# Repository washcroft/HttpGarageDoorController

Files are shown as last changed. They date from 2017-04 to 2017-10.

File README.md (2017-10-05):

# HttpGarageDoorController (v2)
A project for an Arduino based WiFi-enabled controller, IoT/M2M enabling an ordinary garage door operator.

Demo

# About
This Arduino project allows you to directly control your garage door and/or light with HTTP requests, it exposes a very basic REST JSON API via its listening HTTP web server. Since security is important here, both API Key header and **[OAuth 1.0a](https://oauth.net/core/1.0a/) signing/authentication** is supported.

I've used a [MKR1000](https://www.arduino.cc/en/Main/ArduinoMKR1000) board which uses the [WiFi101](https://github.com/arduino-libraries/WiFi101) library, however the project also supports compilation for [ESP8266](https://en.wikipedia.org/wiki/ESP8266) boards.

The Arduino controller toggles GPIO outputs to operate the garage door (using either two separate open/close relays, or more commonly cycling the same one) and also a third output to control the garage light (another relay).

The Arduino controller also uses GPIO inputs to report the state of the garage door (two inputs from separate open/closed reed switches) and also a third input to allow the garage light to be controlled via another source (i.e. the garage door operator itself).

### HomeBridge (Apple HomeKit)
My [HomeBridge](https://github.com/nfarina/homebridge) plugin which accompanies this Arduino project can be found at [homebridge-http-garagedoorcontroller](https://github.com/washcroft/homebridge-http-garagedoorcontroller).

# Configuration

The controller is configured in the **config.h** file:

```
// Controller Config
const char MDNS_NAME[] = "garagedoorcontroller";
const char FRIENDLY_NAME[] = "Garage Door Controller";
const long DOOR_OUTPUT_PULSE_TIME = 400;
const long DOOR_OUTPUT_PULSE_DELAY_TIME = 1250;
const long DOOR_SENSOR_REACT_TIME = 3000;
const long DOOR_MAX_OPEN_CLOSE_TIME = 25000;
const long DOOR_AUTO_CLOSE_TIME = 300000;

// GPIO Pins
const int LED_OUTPUT_PIN = LED_BUILTIN;
const int DOOR_OUTPUT_OPEN_PIN = 3;
const int DOOR_OUTPUT_CLOSE_PIN = 3;
const int LIGHT_OUTPUT_PIN = 2;
const int LIGHT_INPUT_PIN = 1;
const int SENSOR_OPEN_INPUT_PIN = 5;
const int SENSOR_CLOSED_INPUT_PIN = 4;

// ADVANCED - DEFAULTS ARE NORMALLY OK
// Network Config
const long HTTP_SERVER_PORT = 80;
const long HTTP_REQUEST_TIMEOUT = 4000;
const long HTTP_REQUEST_BUFFER_SIZE = 512;
const long WIFI_CONNECTION_TIMEOUT = 10000;

// OAuth Config
const uint16_t OAUTH_NONCE_SIZE = 24;
const uint16_t OAUTH_NONCE_HISTORY = 255;
const uint16_t OAUTH_TIMESTAMP_VALIDITY_WINDOW = 300000;
```

### Variables:

* MDNS_NAME

  The mDNS hostname the controller should publish (exclude .local)

* FRIENDLY_NAME

  The friendly name for the controller

* DOOR_OUTPUT_PULSE_TIME

  The amount of time in milliseconds the GPIO output is kept HIGH when operated (simulated button press)

* DOOR_OUTPUT_PULSE_DELAY_TIME

  The amount of time in milliseconds to wait before the garage door operator will respond to a second triggering of the GPIO output

* DOOR_SENSOR_REACT_TIME

  The amount of time in milliseconds the open/closed sensors take to react to the garage door opening/closing

* DOOR_MAX_OPEN_CLOSE_TIME

  The maximum amount of time in milliseconds the garage door should take to open or close (used to detect a fault status, add a few seconds of margin)

* DOOR_AUTO_CLOSE_TIME

  The maximum amount of time in milliseconds the garage door should be left open before automatically closing, or zero to disable automatic closing (default 300000 = 5 minutes)

* LED_OUTPUT_PIN

  The GPIO output pin connected to the 'network connected' status LED (optional, default LED_BUILTIN)

* DOOR_OUTPUT_OPEN_PIN

  The GPIO output pin connected to the garage door open relay trigger

* DOOR_OUTPUT_CLOSE_PIN

  The GPIO output pin connected to the garage door close relay trigger (set the same as DOOR_OUTPUT_OPEN_PIN if the operator doesn't use separate open/close triggers)

* LIGHT_OUTPUT_PIN

  The GPIO output pin connected to the garage light relay trigger

* LIGHT_INPUT_PIN

  The GPIO input pin connected to the external garage light trigger (optional)

* SENSOR_OPEN_INPUT_PIN

  The GPIO input pin connected to the reed switch at the garage door open position

* SENSOR_CLOSED_INPUT_PIN

  The GPIO input pin connected to the reed switch at the garage door closed position

* HTTP_SERVER_PORT

  The TCP port the HTTP web server should listen on (default 80)

* HTTP_REQUEST_TIMEOUT

  The amount of time in milliseconds a request is allowed to take before closing it (default 4000)

* HTTP_REQUEST_BUFFER_SIZE

  The buffer size to allocate for each incoming HTTP request (default 512)

* WIFI_CONNECTION_TIMEOUT

  The amount of time in milliseconds a WiFi connection can wait to setup before retrying (default 10000)

* OAUTH_NONCE_SIZE

  The size of nonces to retain in memory to prevent replay attacks (default 24)

* OAUTH_NONCE_HISTORY

  The number of nonces to retain in memory to prevent replay attacks (default 255)

* OAUTH_TIMESTAMP_VALIDITY_WINDOW

  The amount of time drift allowed when validating timestamps, since the controller and requester's clocks won't be in exact sync (default 300000 = 5 minutes)

You will also need to add a **secret.h** file to your project containing your sensitive configuration:

```
const char WIFI_SSID[] = "WiFi";
const char WIFI_PASSWORD[] = "MyPassword";
const char OTA_UPDATER_PASSWORD[] = "MyPassword";

const char HTTP_SERVER_APIKEY_HEADER[] = "MyPassword";

const char HTTP_SERVER_OAUTH_CONSUMER_KEY[] = "MyOAuthConsumerKey";
const char HTTP_SERVER_OAUTH_CONSUMER_SECRET[] = "MyOAuthConsumerSecret";
```

### Variables:

* WIFI_SSID

  The WiFi network SSID to connect to

* WIFI_PASSWORD

  The WiFi network password to authenticate the connection

* OTA_UPDATER_PASSWORD

  The password which unlocks over-the-air (OTA) firmware updating in the Arduino IDE

* HTTP_SERVER_APIKEY_HEADER

  The API key which must exist in the X-API-Key HTTP header to authenticate the request (optional, 32 alphanumeric characters recommended or empty string to disable)

* HTTP_SERVER_OAUTH_CONSUMER_KEY

  The OAuth consumer key to be used for OAuth authentication and signing, similar to a username (optional, 32 alphanumeric characters recommended or empty string to disable)

* HTTP_SERVER_OAUTH_CONSUMER_SECRET

  The OAuth consumer secret to be used for OAuth authentication and signing, similar to a password (optional, 64 alphanumeric characters recommended or empty string to disable)

# Debugging

Debug logging can be enabled in the **compile.h** file:

```
#define LOG_LEVEL 0 // ERROR = 1, INFO = 2, DEBUG = 3, VERBOSE = 4, TRACE = 5
```

Increasing the LOG_LEVEL will increase the amount of Serial output to assist with debugging. Ensure this is set back to 0 for production deployment to conserve resources.

# Example Circuit Diagram

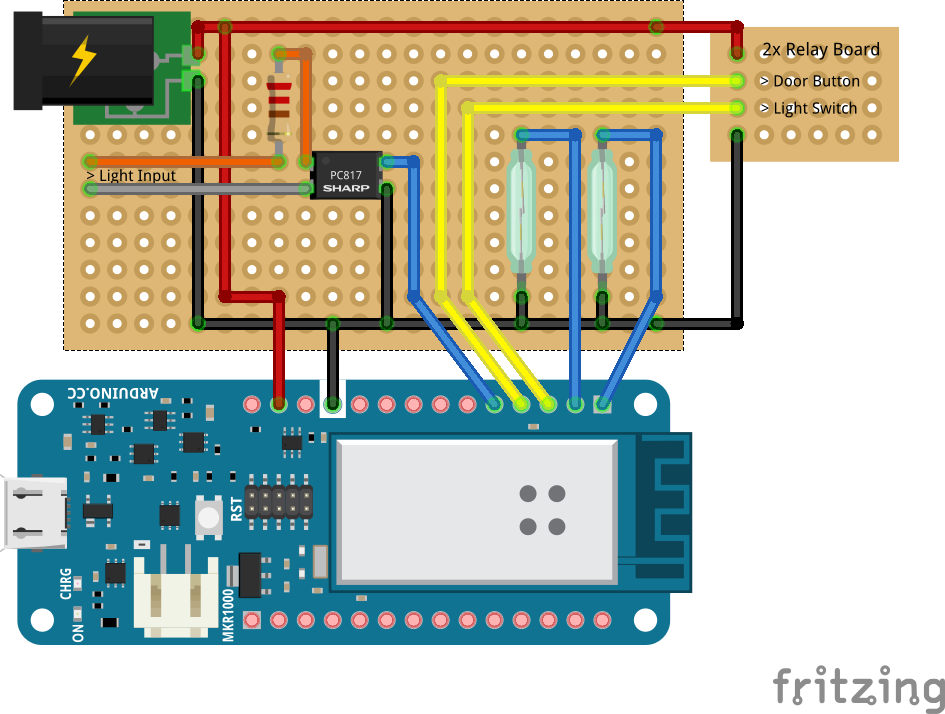
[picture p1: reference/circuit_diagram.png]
Example Circuit Diagram


# REST API Documentation

If the *HTTP_SERVER_APIKEY_HEADER* variable defined in your *secret.h* file is set, all API requests must include the HTTP header **X-API-Key** with that value.

If the *HTTP_SERVER_OAUTH_CONSUMER_KEY* and *HTTP_SERVER_OAUTH_CONSUMER_SECRET* variables defined in your *secret.h* file are set, all API requests must include the OAuth signing parameters in the querystring.

The returned content type will always be **application/json**.

**Note:** It is always recommended to use OAuth to maintain high security, otherwise intercepted HTTP requests on the network would reveal security keys and passwords that could be reused at a later date. Intercepted HTTP requests authorised with OAuth don't reveal any secrets and the same request (i.e. open door) cannot be "replayed" at a later date.

There are plenty of OAuth clients and libraries available, particularly for communicating with the Twitter API as it uses the same scheme. See Twitter developer documentation "[Creating a signature](https://developer.twitter.com/en/docs/basics/authentication/guides/creating-a-signature)".

**Device Info**
----
Returns a JSON payload reporting various running parameters.

* **URL**

  /device

* **Method:**

  `GET`
  
* **URL Params**

  None

* **Success Response:**

  * **Code:** 200 OK <br />
    **Content:**
    
    ```json
    {
      "mdns": "garagedoorcontroller",
      "name": "Garage Door Controller",
      "model": "GARAGEDOOR",
      "firmware": "2.0.0",
      "ip": "10.0.1.152",
      "mac": "ab:3d:f5:aa:a0:22"
    }
    ```
	
**Controller Status**
----
Returns a JSON payload reporting various input/output states.

* **URL**

  /controller

* **Method:**

  `GET`
  
* **URL Params**

  None

* **Success Response:**

  * **Code:** 200 OK <br />
    **Content:**
    
    ```json
    {
      "result": 200,
      "success": true,
      "message": "OK",
      "light-input": false,
      "light-requested": false,
      "light-state": false,
      "sensor-open": false,
      "sensor-closed": false,
      "door-state": "closing"
    }
    ```
 
* **Error Response:**

  * **Code:** 401 Unauthorized <br />
    **Content:**
    
    ```json
    {
      "result": 401,
      "success": false,
      "message": "The requested resource was unauthorized."
    }
    ```

**Control Door**
----
Controls the configured door GPIO output pin with a brief pulse (pulse time configured with *DOOR_OUTPUT_PULSE_TIME*).

* **URL**

  /controller/door/:action

* **Method:**

  `PUT`
  
* **URL Params**

   **Required:**

   `action=[open|close]`

* **Success Response:**

  * **Code:** 202 Accepted <br />
    **Content:**
    
    ```json
    {
      "result": 202,
      "success": true,
      "message": "Accepted"
    }
    ```
 
* **Error Response:**

  * **Code:** 401 Unauthorized <br />
    **Content:**
    
    ```json
    {
      "result": 401,
      "success": false,
      "message": "The requested resource was unauthorized."
    }
    ```

**Control Light**
----
Controls the configured light GPIO output pin and latches.

*Note: If the configured light GPIO input pin is HIGH, it will always override this.*

* **URL**

  /controller/light/:action

* **Method:**

  `PUT`
  
* **URL Params**

   **Required:**

   `action=[on|off]`

* **Success Response:**

  * **Code:** 202 Accepted <br />
    **Content:**
    
    ```json
    {
      "result": 202,
      "success": true,
      "message": "Accepted"
    }
    ```
 
* **Error Response:**

  * **Code:** 401 Unauthorized <br />
    **Content:**
    
    ```json
    {
      "result": 401,
      "success": false,
      "message": "The requested resource was unauthorized."
    }
    ```

# Dependencies, Credits and Licensing
### MKR1000:
- [WiFi101](https://github.com/arduino-libraries/WiFi101) (Copyright (c) Arduino LLC. All right reserved. - GNU LGPL v2.1)
- [WiFi101OTA](https://github.com/arduino-libraries/WiFi101OTA) (Copyright (c) Arduino LLC. All right reserved. - GNU LGPL v2.1)

**Note:** WiFi101OTA does not currently support mDNS hostname resolution, so you will only be able to access the controller via its IP address. I have submitted [Pull Request #3](https://github.com/arduino-libraries/WiFi101OTA/pull/3) for this feature to be included, until then you may choose to [use my version](https://github.com/washcroft/WiFi101OTA/tree/mDNSResponder).

### ESP8266:
- [Arduino for ESP8266](https://github.com/esp8266/Arduino) (Copyright (c) Various. All right reserved. - GNU LGPL v2.1)
- [ArduinoOTA](https://github.com/esp8266/Arduino/tree/master/libraries/ArduinoOTA) (Copyright (c) Various. All right reserved. - GNU LGPL v2.1)

### Libraries:
- [ArduinoJson](https://github.com/bblanchon/ArduinoJson) (Copyright (c) 2014-2017 Benoit BLANCHON - MIT)
- [Bounce2](https://github.com/thomasfredericks/Bounce2) (Copyright (c) 2013 thomasfredericks - MIT)

### Bundled:
- [Sha](https://github.com/Cathedrow/Cryptosuite) (Peter Knight - Public Domain)
- [Base64](https://github.com/adamvr/arduino-base64) (Copyright (c) 2013 Adam Rudd - MIT)
- [HashMap](https://github.com/WiringProject/Wiring/tree/master/framework/libraries/HashMap) (Copyright (c) 2011 Alexander Brevig - GNU LGPL v3.0)
- Clock (Copyright (c) 2017 Warren Ashcroft - MIT)
- HttpWebServer (Copyright (c) 2017 Warren Ashcroft - MIT)
- Utilities (Copyright (c) 2017 Warren Ashcroft - MIT)
- WiFiHelper (Copyright (c) 2017 Warren Ashcroft - MIT)

# License
```
MIT License

Copyright (c) 2017 Warren Ashcroft

Permission is hereby granted, free of charge, to any person obtaining a copy
of this software and associated documentation files (the "Software"), to deal
in the Software without restriction, including without limitation the rights
to use, copy, modify, merge, publish, distribute, sublicense, and/or sell
copies of the Software, and to permit persons to whom the Software is
furnished to do so, subject to the following conditions:

The above copyright notice and this permission notice shall be included in all
copies or substantial portions of the Software.

THE SOFTWARE IS PROVIDED "AS IS", WITHOUT WARRANTY OF ANY KIND, EXPRESS OR
IMPLIED, INCLUDING BUT NOT LIMITED TO THE WARRANTIES OF MERCHANTABILITY,
FITNESS FOR A PARTICULAR PURPOSE AND NONINFRINGEMENT. IN NO EVENT SHALL THE
AUTHORS OR COPYRIGHT HOLDERS BE LIABLE FOR ANY CLAIM, DAMAGES OR OTHER
LIABILITY, WHETHER IN AN ACTION OF CONTRACT, TORT OR OTHERWISE, ARISING FROM,
OUT OF OR IN CONNECTION WITH THE SOFTWARE OR THE USE OR OTHER DEALINGS IN THE
SOFTWARE.
```

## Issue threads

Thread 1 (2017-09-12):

Software for ESP8266 NodeMCU

Diederik98, 2017-09-12:
Hi,

Thanks for your great plugin and arduino code! I copied your version and adjusted it to use it with an ESP8266. I also added OTA support.

I'll post it as attachment.

Kind regards!

[OTA ESP8266 http garagedoor.zip](https://github.com/washcroft/HttpGarageDoorController/files/1297360/OTA.ESP8266.http.garagedoor.zip)

jeylites, 2017-09-22:
@Diederik98

Thanks for the ESP8266 support. I tried to compile today but was stoped with an error. I seem to be missing a Tasker.h file.

Build options changed, rebuilding all
/Users/Documents/Arduino/ESP8266_HTTP_OTA_GARAGEDOOR/ESP8266_HTTP_OTA_GARAGEDOOR.ino:8:20: fatal error: Tasker.h: No such file or directory
 #include <Tasker.h>
                    ^
compilation terminated.
exit status 1
Error compiling for board Generic ESP8266 Module.

Diederik98, 2017-09-22:
Glad you liked it!

You have to add the library first.
You can find it on the main page under Dependencies.

Tasker, Bounce have to be installed. I'm not sure ArduinoJson is one of the standard libraries. Otherwise you also need to install that library.

jeylites, 2017-09-22:
I included the library through Arduino Manage library. It complies but I don't see any MQTT traffic on serial monitor.

I see it has created a device in my router. The web page shows the following.

{ "result": 401, "success": false, "message": "The requested resource was unauthorised." }

Diederik98, 2017-09-22:
I always tested it with the homebridge accessory, because I don't know that much about http headers. Use same api key and check the homebridge log. Have you uncommented '#define DEBUG 1' in your code? Try to use a print statement when the garage is opened and toggle it with your accessory on your iOS device.

jeylites, 2017-09-22:
I uncommented #define DEBUG 1 and I was able to see the MQTT messages. It's working now.

I just want to confirm the pins connection below. I connect a relay to light & door, the light works however not the door.

What are the #define numbers corresponding to e.g.: #define D1 5 ?

DOOR RELAY OPEN/CLOSE = D2
SENSOR REED SWITCH OPEN = D8
SENSOR REED SWITCH CLOSE = D0
LIGHT = D4

Sketch "
#define D0 16
#define D1 5
#define D2 4
#define D3 0
#define D4 2
#define D5 14
#define D6 12
#define D7 13
#define D8 15
#define D9 3
#define D10 1
// LED ON ESP8266 on D4 or GPIO 2
const int LED_OUTPUT_PIN = D4;
const int DOOR_OUTPUT_OPEN_PIN = D2;
const int DOOR_OUTPUT_CLOSE_PIN = D2;
const int LIGHT_OUTPUT_PIN = D4;
const int LIGHT_INPUT_PIN = D1;
// not used, but I gave it a random pin, I did not want to change the code that much.
const int SENSOR_OPEN_INPUT_PIN = D8;
const int SENSOR_CLOSED_INPUT_PIN = D0;
"

Diederik98, 2017-09-26:
I'm sorry for my late answer. I hope it's working now! I used a NodeMCU ESP8266 and each pin had a label. I did that to make the wiring for my device easier.
I think the sensor is HIGH when opened, just print the value to be sure.

washcroft, 2017-10-04:
Thank you Diederik98. I have just released v2.0.0 of this project which includes support for ESP8266 boards (and more).

Closed 2017-10-04.

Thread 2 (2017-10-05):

Error compiling - Secret.h

jeylites, 2017-10-05:
Is my secret.h file correct?

**Secret.h**

const char WIFI_SSID[] = "HELLO";
const char WIFI_PASSWORD[] = "12345678";
const char OTA_UPDATER_PASSWORD[] = "12345678";

const char HTTP_SERVER_APIKEY_HEADER[] = "12345678";

const char HTTP_SERVER_OAUTH_CONSUMER_KEY[] = "HELLO";
const char HTTP_SERVER_OAUTH_CONSUMER_SECRET[] = "ROUTER";

**ERROR MESSAGE**
`Arduino: 1.8.3 (Mac OS X), Board: "Generic ESP8266 Module, Serial, 80 MHz, 40MHz, DOUT, 115200, 1M (no SPIFFS), ck, Disabled, None"

In file included from sketch/GarageDoorController.h:14:0,
                 from /Users/J/Documents/Arduino/Portable/HttpGarageDoorController/HttpGarageDoorController.ino:46:
secret.h:1: error: redefinition of 'const char WIFI_SSID []'
 const char WIFI_SSID[] = "HELLO";
                      ^
In file included from /Users/J/Documents/Arduino/Portable/HttpGarageDoorController/HttpGarageDoorController.ino:44:0:
secret.h:1: error: 'const char WIFI_SSID [6]' previously defined here
 const char WIFI_SSID[] = "HELLO";
            ^
In file included from sketch/GarageDoorController.h:14:0,
                 from /Users/J/Documents/Arduino/Portable/HttpGarageDoorController/HttpGarageDoorController.ino:46:
secret.h:2: error: redefinition of 'const char WIFI_PASSWORD []'
 const char WIFI_PASSWORD[] = "12345678";
                          ^
In file included from /Users/J/Documents/Arduino/Portable/HttpGarageDoorController/HttpGarageDoorController.ino:44:0:
secret.h:2: error: 'const char WIFI_PASSWORD [9]' previously defined here
 const char WIFI_PASSWORD[] = "12345678";
            ^
In file included from sketch/GarageDoorController.h:14:0,
                 from /Users/J/Documents/Arduino/Portable/HttpGarageDoorController/HttpGarageDoorController.ino:46:
secret.h:3: error: redefinition of 'const char OTA_UPDATER_PASSWORD []'
 const char OTA_UPDATER_PASSWORD[] = "12345678";
                                 ^
In file included from /Users/J/Documents/Arduino/Portable/HttpGarageDoorController/HttpGarageDoorController.ino:44:0:
secret.h:3: error: 'const char OTA_UPDATER_PASSWORD [9]' previously defined here
 const char OTA_UPDATER_PASSWORD[] = "12345678";
            ^
In file included from sketch/GarageDoorController.h:14:0,
                 from /Users/J/Documents/Arduino/Portable/HttpGarageDoorController/HttpGarageDoorController.ino:46:
secret.h:5: error: redefinition of 'const char HTTP_SERVER_APIKEY_HEADER []'
 const char HTTP_SERVER_APIKEY_HEADER[] = "12345678";
                                      ^
In file included from /Users/J/Documents/Arduino/Portable/HttpGarageDoorController/HttpGarageDoorController.ino:44:0:
secret.h:5: error: 'const char HTTP_SERVER_APIKEY_HEADER [9]' previously defined here
 const char HTTP_SERVER_APIKEY_HEADER[] = "12345678";
            ^
In file included from sketch/GarageDoorController.h:14:0,
                 from /Users/J/Documents/Arduino/Portable/HttpGarageDoorController/HttpGarageDoorController.ino:46:
secret.h:7: error: redefinition of 'const char HTTP_SERVER_OAUTH_CONSUMER_KEY []'
 const char HTTP_SERVER_OAUTH_CONSUMER_KEY[] = "HELLO";
                                           ^
In file included from /Users/J/Documents/Arduino/Portable/HttpGarageDoorController/HttpGarageDoorController.ino:44:0:
secret.h:7: error: 'const char HTTP_SERVER_OAUTH_CONSUMER_KEY [6]' previously defined here
 const char HTTP_SERVER_OAUTH_CONSUMER_KEY[] = "HELLO";
            ^
In file included from sketch/GarageDoorController.h:14:0,
                 from /Users/J/Documents/Arduino/Portable/HttpGarageDoorController/HttpGarageDoorController.ino:46:
secret.h:8: error: redefinition of 'const char HTTP_SERVER_OAUTH_CONSUMER_SECRET []'
 const char HTTP_SERVER_OAUTH_CONSUMER_SECRET[] = "ROUTER";
                                              ^
In file included from /Users/J/Documents/Arduino/Portable/HttpGarageDoorController/HttpGarageDoorController.ino:44:0:
secret.h:8: error: 'const char HTTP_SERVER_OAUTH_CONSUMER_SECRET [7]' previously defined here
 const char HTTP_SERVER_OAUTH_CONSUMER_SECRET[] = "ROUTER";
            ^
exit status 1
redefinition of 'const char WIFI_SSID []'

This report would have more information with
"Show verbose output during compilation"
option enabled in File -> Preferences.
`

washcroft, 2017-10-05:
This was caused by the **secret.h** file being included twice within the project, this is now fixed.

jeylites, 2017-10-05:
Will test it again :)

Closed 2017-10-05.

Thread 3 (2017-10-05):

Unable to debug & D1 Mini GPIO

jeylites, 2017-10-05:
Unable to see if device connected to the router or not, previously, I was able to see the messages after  uncommented '#define DEBUG

Here is the changes I made...
#define LOG_LEVEL 3 // ERROR = 1, INFO = 2, DEBUG = 3, VERBOSE = 4, TRACE = 5

**Baud: 115200**
ets Jan  8 2013,rst cause:4, boot mode:(3,6)

wdt reset
load 0x4010f000, len 1384, room 16
tail 8
chksum 0x2d
csum 0x2d
v3de0c112
~ld

I'm currently using a Wemos D1 mini for this project,
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

Are the GPIO pin the same as the sketch

// GPIO Pins
const uint8_t LED_OUTPUT_PIN = LED_BUILTIN;
const uint8_t DOOR_OUTPUT_OPEN_PIN = 3;
const uint8_t DOOR_OUTPUT_CLOSE_PIN = 3;
const uint8_t LIGHT_OUTPUT_PIN = 2;
const uint8_t LIGHT_INPUT_PIN = 1;
const uint8_t SENSOR_OPEN_INPUT_PIN = 5;
const uint8_t SENSOR_CLOSED_INPUT_PIN = 4;

washcroft, 2017-10-05:
Hello,
The pins in the example config won't work on the ESP8266, as they're what I used on a MKR1000. That's why it's currently crashing, before it's even started during pin setup.

I have just tested this with Wemos D1 mini, and here are some example pins that work for that board:

```
// GPIO Pins
const uint8_t LED_OUTPUT_PIN = LED_BUILTIN;
const uint8_t DOOR_OUTPUT_OPEN_PIN = D1;     // D1 = pin 16
const uint8_t DOOR_OUTPUT_CLOSE_PIN = D1;    // D1 = pin 16
const uint8_t LIGHT_OUTPUT_PIN = D2;         // D2 = pin 4
const uint8_t LIGHT_INPUT_PIN = D5;          // D5 = pin 14
const uint8_t SENSOR_OPEN_INPUT_PIN = D6;    // D6 = pin 12
const uint8_t SENSOR_CLOSED_INPUT_PIN = D7;  // D7 = pin 13
```

Best Regards,
Warren

Closed 2017-10-06.

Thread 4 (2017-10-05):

API Key header authorization FAILURE - header mismatch & Trigger Hi/Lo

jeylites, 2017-10-05:
I'm making progress washcroft... I'm currently stuck on the API key header authentication

What is the relation for the following

```
HTTP_SERVER_APIKEY_HEADER[] = "MyOAuthConsumerKey";
HTTP_SERVER_OAUTH_CONSUMER_KEY[] = "MyOAuthConsumerKey";
HTTP_SERVER_OAUTH_CONSUMER_SECRET[] = "MyOAuthConsumerSecret";
```

AND

```
"httpHeaderName": "MyPassword",
"httpHeaderValue": "MyPassword",

```

WiFi Connection Lost - Connecting
Finding WiFi hardware......found!
Connecting to WiFi network...{"result":200,"success":true,"message":"OK","light-input":false,"light-requested":false,"light-state":false,"sensor-open":true,"sensor-closed":false,"door-state":"open"}
{"result":200,"success":true,"message":"OK","light-input":false,"light-requested":false,"light-state":false,"sensor-open":true,"sensor-closed":false,"door-state":"open"}
connected to HELLO
Obtaining IP address...obtained 192.xxx.xxx.xxx
WiFi Connection Complete

SSID: HELLO
Signal Strength (RSSI): -63 dBm
Client MAC: xc:cf:xf:fx:bx:ex
Station MAC: ax:bx:ex:ec:5x:ce
Client IP Address: 192.xxx.xxx.xxx
Gateway IP Address: 192.xxx.xxx.xxx
mDNS Hostname: garagedoorcontroller.local

Starting OTA updater / mDNS responderStarting HTTP web server...started!
Initalising clock...initalised at 2017-10-05 17:16:28 UTC
{"result":200,"success":true,"message":"OK","light-input":false,"light-requested":false,"light-state":false,"sensor-open":true,"sensor-closed":false,"door-state":"open"}
{"result":200,"success":true,"message":"OK","light-input":false,"light-requested":false,"light-state":false,"sensor-open":true,"sensor-closed":false,"door-state":"open"}

Accepted new client connection from 192.xxx.xxx.xxx:49178
GET /controller HTTP/1.1
MyOAuthConsumerKey: MyOAuthConsumerKey
host: garagedoorcontroller.local
Connection: close

**API Key header authorisation FAILURE - header mismatch**
HTTP/1.1 401 Unauthorized
Content-Type: application/json
Connection: close

**Secret.h**
```
const char WIFI_SSID[] = "HELLO";
const char WIFI_PASSWORD[] = "12345678";
const char OTA_UPDATER_PASSWORD[] = "MyPassword";

const char HTTP_SERVER_APIKEY_HEADER[] = "MyOAuthConsumerKey";

const char HTTP_SERVER_OAUTH_CONSUMER_KEY[] = "MyOAuthConsumerKey";
const char HTTP_SERVER_OAUTH_CONSUMER_SECRET[] = "MyOAuthConsumerSecret";

```

**Homebridge Config.**

```
{
	"accessories": [{
		"accessory": "HttpGarageDoorController",
		"name": "Garage Door",
		"lightName": "Garage Light",

		"doorOperationSeconds": 0,

		"httpHost": "garagedoorcontroller.local",
		"httpPort": 80,
		"httpSsl": false,
		"httpStatusPollMilliseconds": 4000,
		"httpRequestTimeoutMilliseconds": 10000,

		"httpHeaderName": "MyPassword",
		"httpHeaderValue": "MyPassword",

		"oauthAuthentication": true,
		"oauthSignatureMethod": "HMAC-SHA256",
		"oauthConsumerKey": "MyOAuthConsumerKey",
		"oauthConsumerSecret": "MyOAuthConsumerSecret",
		"oauthToken": "MyOAuthToken",
		"oauthTokenSecret": "MyOAuthTokenSecret",

		"apiConfig": {
			"apiType": "HttpGarageDoorController"
		}
	}]
}

```

washcroft, 2017-10-05:
When using the HomeBridge module with this Arduino project, ```httpHeaderName``` should be "X-API-Key" - this isn't clear so I'll add that to the docs.

```oauthConsumerKey``` and ```oauthConsumerSecret``` should match in both HomeBridge module and Arduino project.

```oauthToken``` and ```oauthTokenSecret``` should be empty "" because they're not using in the Arduino project.

jeylites, 2017-10-06:
@washcroft

After some tinkering, I manage to get it working. The APIKEY HEADER threw me off. I was thinking "MyPassword" was supposed to be the same password as OTA in the Arduino secret.h sketch but what it really meant was "MyAPIKey".

```
**Secret.h**
const char HTTP_SERVER_APIKEY_HEADER[] = "MyPassword";
**Config.json**
"httpHeaderValue": "MyAPIKey"

```
**RELAY hi/lo trigger**
Is there a way to set the relay outputs to LOW-level trigger. The reason I'm asking is that the relays go from HI to LO after the Wemmos D1 mini comes out from a power cycle or reset which in turn opens the garage door.

**API**
What are the Json API and Generic / Plain API usage and difference?

**Timings**
`DOOR_SENSOR_REACT_TIME` & `DOOR_MAX_OPEN_CLOSE_TIME `

Should REACT time be the same or as MAX time or by half?
React time do you mean as how fast the state changes from one or the other?

Thank you.

washcroft, 2017-10-08:
> Is there a way to set the relay outputs to LOW-level trigger. The reason I'm asking is that the relays go from HI - LO - HI after the Wemmos D1 mini comes out from a power cycle or reset which in turn opens the garage door.

The controller brings the relay pin ```HIGH``` for the ```DOOR_OUTPUT_PULSE_DELAY_TIME``` time and then puts it back ```LOW``` (to simulate a button press). How are you connecting it to your motor controller if LOW triggers it?

> What are the Json API and Generic / Plain API usage and difference?

The homebridge-http-garagedoorcontroller is designed to support other integrations, but if you're using this HttpGarageDoorController project, you don't need to use those since setting ```apiType``` to HttpGarageDoorController configures the API correctly.

> Should REACT time be the same or as MAX time or by half?

Some door open/closed sensors "bounce" or "flicker" when changing state (i.e. magnetic reed switches), the ```DOOR_SENSOR_REACT_TIME``` setting sets how long the sensors have to settle in their current state before using their values.

```DOOR_MAX_OPEN_CLOSE_TIME``` sets how long the motor usually takes to open or close the door. If the door hasn't completely opened or closed during this time (as indicated by the sensors), then the controller can report the door the "stopped" moving and is therefore left partially open.

> Lastly, On Homebridge to change the Icon from a garage to a switch, do I change the MDNS NAME & FRIENDLY to = lock or switch?

No, these fields just identify the devices on the network. Currently, the module will always report the unit to HomeKit as a "Garage Door service". This may change with a feature update soon.

jeylites, 2017-10-08:
Is there a way to set the relay outputs to LOW-level trigger. The reason I'm asking is that the relays go from HI - LO - HI after the Wemmos D1 mini comes out from a power cycle or reset which in turn opens the garage door.

> The controller brings the relay pin HIGH for the DOOR_OUTPUT_PULSE_DELAY_TIME time and then puts it back LOW (to simulate a button press). How are you connecting it to your motor controller if LOW triggers it?

Currently, I have my hardware setup the same way as yours except I'm using the Wemmos D1.

Everything works fine - except the relay triggers everytime the unit  restarts - causing my garage door to open (relay is connected to garage door push button {open/close} )

The relay is in a 'high' state during normal operation, so when the power goes out, it triggered the relay.

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

The kind of relay I'm using [RELAY](http://www.ebay.co.uk/itm/5V-1-2-4-8-Channel-Relay-Board-Module-for-Arduino-Raspberry-Pi-ARM-AVR-DSP-PIC-/252051910091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

washcroft, 2017-10-08:
I use a similar relay board.
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
jeylites, 2017-10-08:
I tried the jumper, it’s nothing more than an enable or disable relay
feature.

I also tried a new D1 and Relay board, the behavior still exists.

I’m wondering if would it fix the issue if get a relay with  hi/lo option.

On Sun, Oct 8, 2017 at 7:32 PM Warren Ashcroft <notifications@github.com>
wrote:

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
--
Sent from Iphone Mobile

washcroft, 2017-10-08:
> I’m wondering if would it fix the issue if get a relay with  hi/lo option.

I updated my reply on the GitHub issue. However, this is what you need to do, use a different type of relay board which you can trigger (energise) the relay with 3.3v HIGH.

washcroft, 2017-10-08:
> I’m wondering if would it fix the issue if get a relay with  hi/lo option.

I updated my reply on the GitHub issue. However, this is what you need to do, use a different type of relay board which you can trigger (energise) the relay with 3.3v HIGH.

Previous reply:

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

jeylites, 2017-10-08:
I have made some developments. Because the relay module operates on 5V and ESP8266 operate on 3.3V, I used a 2N2222 NPN transistor to shift levels,  like the circuit below. So now the relay only energize when Open or Close is pushed on homekit App.

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

You mentioned there is a way to permanently invert the trigger in the code, what changes should I make?

```
    digitalWrite(pin, HIGH);
    delay(DOOR_OUTPUT_PULSE_TIME);
    digitalWrite(pin, LOW);
```

The other problem is to prevent the relay to trigger upon ESP8266 startup. This translates to the gate opening or closing. I was looking into a delay circuitry which is tied to trigger relay VCC. Its little overkill but it works.

just wondering, Is there a way to do this in the code?

jeylites, 2017-10-08:
Another update on relay triggering upon startup. Turns out, it's a common problem with these ESP8266. Some guy in blog suggested to put a 10k on the gpio pin (D1)  then other end of resistor to ground for pulldown.

Everything work as it should be now. I'm still going to get a 3.3 relay as well. Also I was looking at the SSR, which does 3V to 32VDC  [Solid State Relays ](http://www.ebay.com/itm/SSR-25-DA-25A-DC-AC-24V-380V-Solid-State-Relay-for-PID-Temperature-Controller-/191989321890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)

washcroft, 2017-10-08:
1) Getting a 3.3v HIGH triggered relay would be my preferred option; or

2) Alter the circuit as you suggested, although I suspect it'd be easier to alter the relay board, simply by swapping around the input connections to the optoisolator); or

3) Alter the code:

https://github.com/washcroft/HttpGarageDoorController/blob/master/GarageDoorController.cpp#L33

becomes:

```
digitalWrite(pin, LOW);
delay(DOOR_OUTPUT_PULSE_TIME);
digitalWrite(pin, HIGH);
```

You might also need to add this line here, so that the trigger is HIGH at boot:

https://github.com/washcroft/HttpGarageDoorController/blob/master/GarageDoorController.cpp#L59

```
digitalWrite(DOOR_OUTPUT_OPEN_PIN, HIGH);
```

jeylites, 2017-10-08:
The changes you suggested worked. I no longer need the pulldown and the relay is triggering right. However, I'm going to purchase the 3.3V type High trigger just to keep it safe.

Thank you Warren!

washcroft, 2017-10-08:
No problem :)

rjblake, 2018-03-04:
I have the same/similar 2-way relay and the same problem. I've amended code for the door relay and it seems to work ok, but the light relay always gets pulled low and turned on at boot/restart. I guess I'll have to try get hold of another module, but perhaps an enhancement request would be to allow the options as a configuration

jeylites, 2018-03-04:
@rjblake

you should! The last thing you want is to have the garage door fail on you. I got the 3ch as linked below it has worked great ever since. Currently using stock code with the only alteration on output pins to work on Wemos D1 mini.

[1CH 3.3V Relay](https://www.ebay.com/itm/1PCS-3V-Relay-High-Level-Driver-Module-optocouple-Relay-Module-for-Arduino-NEW/381733076159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)

[3CH 3.3V Relay](https://www.ebay.com/itm/3-Channel-Relay-Module-With-Optocoupler-Isolation-Compatible-3-3V-5V-Signal/311751431759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)

washcroft, 2018-03-04:
@rjblake It's not possible to change what happens on the outputs whilst the MCU boots, of course we can control the outputs once it has booted into user code.

For this reason, better to get a module that works the right way around.

rjblake, 2018-03-05:
@washcroft then I’m really confused as previously have the ESP booting with ESPEasy firmware and it boots without any change to relay state; I.e. it remains in off state

Closed 2017-10-08.

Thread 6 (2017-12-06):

don't know how to start the project

FilD201, 2017-12-06:
hi, I don't understand what I specifically need to do to make this work, can you explain which code needs to go where?

washcroft, 2017-12-16:
This is a standard Arduino project, download the whole project, open HttpGarageDoorController.ino in the IDE, configure as per documentation and then upload to your chosen hardware.

sparklingsparklers, 2018-02-18:
@washcroft There is really a lack of said documentation...

washcroft, 2018-02-18:
@sparklingsparklers There is ample documentation in README.md, this is **project specific** documentation, not an introduction to micro controller programming and development.

sparklingsparklers, 2018-02-18:
@washcroft

After downloading the project, creating the secret.h file, and downloading the dependencies, this is the error im getting.

Arduino: 1.8.5 (Mac OS X), Board: "NodeMCU 1.0 (ESP-12E Module), 80 MHz, 4M (1M SPIFFS), v2 Prebuilt (MSS=536), Disabled, None, 115200"

Build options changed, rebuilding all
Archiving built core (caching) in: /var/folders/9q/7t76cjg50vj1hzjh_ygqd6l00000gn/T/arduino_cache_337983/core/core_esp8266_esp8266_nodemcuv2_CpuFrequency_80,FlashSize_4M1M,LwIPVariant_v2mss536,Debug_Disabled,DebugLevel_None____,UploadSpeed_115200_c3854604d461a8e339a634f719585bd3.a
sketch/HttpGarageDoorController.ino.cpp.o:(.text._Z41__static_initialization_and_destruction_0ii$part$0+0x18): undefined reference to `HttpWebServer::~HttpWebServer()'
sketch/HttpGarageDoorController.ino.cpp.o:(.text._Z41__static_initialization_and_destruction_0ii$part$0+0x1c): undefined reference to `WiFiHelper::~WiFiHelper()'
sketch/HttpGarageDoorController.ino.cpp.o: In function `__static_initialization_and_destruction_0':
/var/folders/9q/7t76cjg50vj1hzjh_ygqd6l00000gn/T/arduino_modified_sketch_877919/HttpGarageDoorController.ino:61: undefined reference to `HttpWebServer::~HttpWebServer()'
sketch/HttpGarageDoorController.ino.cpp.o: In function `~WiFiServer':
/Users/alan/Library/Arduino15/packages/esp8266/hardware/esp8266/2.4.0/libraries/ESP8266WiFi/src/WiFiServer.h:50: undefined reference to `WiFiHelper::~WiFiHelper()'
sketch/HttpGarageDoorController.ino.cpp.o:(.text.setup+0x10): undefined reference to `WiFiHelper::enable_led(unsigned char, unsigned char, unsigned char, bool)'
sketch/HttpGarageDoorController.ino.cpp.o:(.text.setup+0x14): undefined reference to `HttpWebServer::enable_apikey_header_auth(char const*)'
sketch/HttpGarageDoorController.ino.cpp.o:(.text.setup+0x18): undefined reference to `HttpWebServer::enable_oauth_auth(UDP&, char const*, char const*, unsigned short, unsigned short, unsigned short)'
sketch/HttpGarageDoorController.ino.cpp.o: In function `setup':
/var/folders/9q/7t76cjg50vj1hzjh_ygqd6l00000gn/T/arduino_modified_sketch_877919/HttpGarageDoorController.ino:76: undefined reference to `WiFiHelper::enable_led(unsigned char, unsigned char, unsigned char, bool)'
/var/folders/9q/7t76cjg50vj1hzjh_ygqd6l00000gn/T/arduino_modified_sketch_877919/HttpGarageDoorController.ino:66: undefined reference to `HttpWebServer::enable_apikey_header_auth(char const*)'
/var/folders/9q/7t76cjg50vj1hzjh_ygqd6l00000gn/T/arduino_modified_sketch_877919/HttpGarageDoorController.ino:83: undefined reference to `HttpWebServer::enable_oauth_auth(UDP&, char const*, char const*, unsigned short, unsigned short, unsigned short)'
/var/folders/9q/7t76cjg50vj1hzjh_ygqd6l00000gn/T/arduino_modified_sketch_877919/HttpGarageDoorController.ino:88: undefined reference to `WiFiHelper::is_connected()'
/var/folders/9q/7t76cjg50vj1hzjh_ygqd6l00000gn/T/arduino_modified_sketch_877919/HttpGarageDoorController.ino:88: undefined reference to `WiFiHelper::connect()'
sketch/HttpGarageDoorController.ino.cpp.o:(.text._Z11connectWiFiv+0x14): undefined reference to `HttpWebServer::begin()'
sketch/HttpGarageDoorController.ino.cpp.o:(.text._Z11connectWiFiv+0x18): undefined reference to `Clock::update(bool)'
sketch/HttpGarageDoorController.ino.cpp.o:(.text._Z11connectWiFiv+0x1c): undefined reference to `Clock::now_utc()'
sketch/HttpGarageDoorController.ino.cpp.o:(.text._Z11connectWiFiv+0x20): undefined reference to `Clock::get_formatted_time(long, char*, unsigned int)'
sketch/HttpGarageDoorController.ino.cpp.o:(.text._Z11connectWiFiv+0x30): undefined reference to `WiFiHelper::is_connected()'
sketch/HttpGarageDoorController.ino.cpp.o: In function `connectWiFi()':
/var/folders/9q/7t76cjg50vj1hzjh_ygqd6l00000gn/T/arduino_modified_sketch_877919/HttpGarageDoorController.ino:96: undefined reference to `WiFiHelper::connect()'
/var/folders/9q/7t76cjg50vj1hzjh_ygqd6l00000gn/T/arduino_modified_sketch_877919/HttpGarageDoorController.ino:108: undefined reference to `HttpWebServer::begin()'
/var/folders/9q/7t76cjg50vj1hzjh_ygqd6l00000gn/T/arduino_modified_sketch_877919/HttpGarageDoorController.ino:109: undefined reference to `Clock::update(bool)'
/var/folders/9q/7t76cjg50vj1hzjh_ygqd6l00000gn/T/arduino_modified_sketch_877919/HttpGarageDoorController.ino:110: undefined reference to `Clock::now_utc()'
/var/folders/9q/7t76cjg50vj1hzjh_ygqd6l00000gn/T/arduino_modified_sketch_877919/HttpGarageDoorController.ino:123: undefined reference to `Clock::get_formatted_time(long, char*, unsigned int)'
sketch/HttpGarageDoorController.ino.cpp.o:(.text._Z17getJsonDeviceInfoPcj+0x30): undefined reference to `WiFiHelper::get_mac(char*, unsigned int)'
sketch/HttpGarageDoorController.ino.cpp.o:(.text._Z17getJsonDeviceInfoPcj+0x34): undefined reference to `WiFiHelper::get_client_ip(char*, unsigned int)'
sketch/HttpGarageDoorController.ino.cpp.o: In function `List':
/Users/alan/Documents/Arduino/libraries/ArduinoJson-master/src/ArduinoJson/Data/List.hpp:30: undefined reference to `WiFiHelper::get_mac(char*, unsigned int)'
/Users/alan/Documents/Arduino/libraries/ArduinoJson-master/src/ArduinoJson/Data/List.hpp:30: undefined reference to `WiFiHelper::get_client_ip(char*, unsigned int)'
sketch/HttpGarageDoorController.ino.cpp.o: In function `StaticStringBuilder':
/Users/alan/Documents/Arduino/libraries/ArduinoJson-master/src/ArduinoJson/Deserialization/../Serialization/StaticStringBuilder.hpp:14: undefined reference to `HttpWebServer::send_response(Client&, unsigned short, unsigned char const*, unsigned int)'
sketch/HttpGarageDoorController.ino.cpp.o: In function `requestHandler(Client&, char const*, char const*, HashMap<char*, char*, 24u>&)':
/var/folders/9q/7t76cjg50vj1hzjh_ygqd6l00000gn/T/arduino_modified_sketch_877919/HttpGarageDoorController.ino:174: undefined reference to `HttpWebServer::send_response(Client&, unsigned short, unsigned char const*, unsigned int)'
/var/folders/9q/7t76cjg50vj1hzjh_ygqd6l00000gn/T/arduino_modified_sketch_877919/HttpGarageDoorController.ino:170: undefined reference to `WiFiHelper::WiFiHelper(char const*, char const*, char const*, unsigned short)'
/var/folders/9q/7t76cjg50vj1hzjh_ygqd6l00000gn/T/arduino_modified_sketch_877919/HttpGarageDoorController.ino:175: undefined reference to `HttpWebServer::HttpWebServer(Server&, unsigned short, unsigned short, unsigned short)'
sketch/HttpGarageDoorController.ino.cpp.o:(.text.startup._GLOBAL__sub_I_gController+0x37): undefined reference to `WiFiHelper::WiFiHelper(char const*, char const*, char const*, unsigned short)'
sketch/HttpGarageDoorController.ino.cpp.o: In function `__static_initialization_and_destruction_0':
/var/folders/9q/7t76cjg50vj1hzjh_ygqd6l00000gn/T/arduino_modified_sketch_877919/HttpGarageDoorController.ino:59: undefined reference to `HttpWebServer::HttpWebServer(Server&, unsigned short, unsigned short, unsigned short)'
sketch/HttpGarageDoorController.ino.cpp.o: In function `_GLOBAL__sub_D_gController':
/var/folders/9q/7t76cjg50vj1hzjh_ygqd6l00000gn/T/arduino_modified_sketch_877919/HttpGarageDoorController.ino:61: undefined reference to `HttpWebServer::poll(Client&, unsigned short (*)(Client&, char const*, char const*, HashMap<char*, char*, 24u>&))'
sketch/HttpGarageDoorController.ino.cpp.o: In function `loop':
/var/folders/9q/7t76cjg50vj1hzjh_ygqd6l00000gn/T/arduino_modified_sketch_877919/HttpGarageDoorController.ino:184: undefined reference to `HttpWebServer::poll(Client&, unsigned short (*)(Client&, char const*, char const*, HashMap<char*, char*, 24u>&))'
libraries/HttpGarageDoorController-master/GarageDoorController.cpp.o: In function `StaticStringBuilder':
/Users/alan/Documents/Arduino/libraries/ArduinoJson-master/src/ArduinoJson/Deserialization/../Serialization/StaticStringBuilder.hpp:13: undefined reference to `striendswith(char const*, char const*)'
libraries/HttpGarageDoorController-master/GarageDoorController.cpp.o: In function `GarageDoorController::requestHandler(Client&, char const*, char const*, HashMap<char*, char*, 24u>&)':
/Users/alan/Documents/Arduino/libraries/HttpGarageDoorController-master/GarageDoorController.cpp:165: undefined reference to `HttpWebServer::send_response(Client&, unsigned short, unsigned char const*, unsigned int)'
/Users/alan/Documents/Arduino/libraries/HttpGarageDoorController-master/GarageDoorController.cpp:172: undefined reference to `striendswith(char const*, char const*)'
/Users/alan/Documents/Arduino/libraries/HttpGarageDoorController-master/GarageDoorController.cpp:179: undefined reference to `striendswith(char const*, char const*)'
/Users/alan/Documents/Arduino/libraries/HttpGarageDoorController-master/GarageDoorController.cpp:182: undefined reference to `striendswith(char const*, char const*)'
/Users/alan/Documents/Arduino/libraries/HttpGarageDoorController-master/GarageDoorController.cpp:187: undefined reference to `striendswith(char const*, char const*)'
collect2: error: ld returned 1 exit status
exit status 1
Error compiling for board NodeMCU 1.0 (ESP-12E Module).

This report would have more information with
"Show verbose output during compilation"
option enabled in File -> Preferences.

Closed 2017-12-16.

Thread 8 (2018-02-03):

Light input?

mattiasclaesson, 2018-02-03:
Hi,

In the example schematics, the light input 12V DC is that from the built in door opener lamp?

The light output is that intended to control the same door opener lamp?

Is it possible to remove the light icon and functionality from being displayed in the homekit so that it is not visible in the app?

washcroft, 2018-02-03:
> In the example schematics, the light input 12V DC is that from the built in door opener lamp?

Yes, it just taps onto the opener's own light (LED in my case - it drives an opto isolator, which provides an isolated input to the Arduino).

> The light output is that intended to control the same door opener lamp?

No, it's intended to connect to a relay to switch on all you main/primary lights in the garage.

> Is it possible to remove the light icon and functionality from being displayed in the homekit so that it is not visible in the app?

Yes, by not configuring the light related config fields.

mattiasclaesson, 2018-02-07:
Ok, I guess its not able to know if the main/primary lights is on or off then.

I did try to remove the  "lightName" but ended up with a exception:

`
/usr/local/lib/node_modules/homebridge-http-garagedoorcontroller/index.js:642                                                                        
                this.garageLightCurrentState.setValue(this._lightCurrentState);                                                                      
                                             ^                                                                                                       
                                                                                                                                                     
TypeError: Cannot read property 'setValue' of undefined                                                                                              
    at HttpGarageDoorControllerAccessory._setLightCurrentState (/usr/local/lib/node_modules/homebridge-http-garagedoorcontroller/index.js:642:32)    
    at /usr/local/lib/node_modules/homebridge-http-garagedoorcontroller/index.js:482:13                                                              
    at /usr/local/lib/node_modules/homebridge-http-garagedoorcontroller/index.js:552:4                                                               
    at Request._callback (/usr/local/lib/node_modules/homebridge-http-garagedoorcontroller/index.js:831:5)                                           
    at Request.self.callback (/usr/local/lib/node_modules/homebridge-http-garagedoorcontroller/node_modules/request/request.js:186:22)               
    at Request.emit (events.js:159:13)                                                                                                               
    at Request.<anonymous> (/usr/local/lib/node_modules/homebridge-http-garagedoorcontroller/node_modules/request/request.js:1163:10)                
    at Request.emit (events.js:159:13)                                                                                                               
    at IncomingMessage.<anonymous> (/usr/local/lib/node_modules/homebridge-http-garagedoorcontroller/node_modules/request/request.js:1085:12)        
    at Object.onceWrapper (events.js:254:19)
`

Maybe there was more to remove then?

rjblake, 2018-02-12:
I'm guessing Warren meant not configuring these (in config.h):
const uint8_t LIGHT_OUTPUT_PIN = 2;
const uint8_t LIGHT_INPUT_PIN = 1;

I'm looking to install this for my setup on an ESP8266, however have a 2x relay board setup (1x for Garage Door, 1x for Lights). Rather than re-cable my opener, would be great if I could control the 2x relays separately (also e.g. if you have 2x garage doors), and use the automation in the Home app to turn on/off the lights depending on state of door. Guess I need to dig into the code (looks great btw and really like the security aspects). I'm also using Domoticz, so hoping the Homebridge/MQTT will keep state in synch

washcroft, 2018-02-12:
I assumed @mattiasclaesson was referring to the [accompanying HomeBridge plugin](https://github.com/washcroft/homebridge-http-garagedoorcontroller) for this, in there you can avoid setting the lightname configuration field and it wont expose a light accessory in HomeKit.

@mattiasclaesson, the "setValue" exception you mentioned is fixed in the latest version of that project:
https://github.com/washcroft/homebridge-http-garagedoorcontroller/issues/8

There is nothing in this project to specifically remove the light related functionality, but simply assign unused pins to the light config and nothing will ever happen.

washcroft, 2018-02-12:
@rjblake
> Rather than re-cable my opener, would be great if I could control the 2x relays separately (also e.g. if you have 2x garage doors)

Currently the project activates two relays, one for your garage door opener button, the other to close/switch a lighting circuit. Are you suggesting an option to replace the light relay with another garage door opener button, for a second garage door? How would you then control the garage light, some other automation/smart bulb system?

It may be a good idea to simply support multiple lights/doors in this project, i.e. as many as GPIO pins you have avaiaible! The API spec would need to change to accomodate "which" door/light being controlled in the request.

rjblake, 2018-02-12:
> Currently the project activates two relays, one for your garage door opener button, the other to close/switch a lighting circuit. Are you suggesting an option to replace the light relay with another garage door opener button, for a second garage door? How would you then control the garage light, some other automation/smart bulb system?
The 'Light Input' on your circuit has me confused - assumed that it uses this input to determine whether to turn on or off. I would not have this input, but just the lighting wired up to the 2nd relay and connected to a GPIO. On/Off for light could either be controlled separately, or made to follow the door status. In the case of the Hormann Supramatic opener, the built in light can be controlled separately, and is also on a timer.

washcroft, 2018-02-12:
Most garage door openers have a built in light, usually this is a small LED and not very bright. By using this as an "input" to the controller, you can have the controller automatically operate the light "output" to switch more lighting on and off (i.e. all your main garage lighting) at the same time as the opener operates its own built in light (normally when it is opening or closing the door).

This input is more of a convenience, it can be triggered by whatever you like (caution: with the correct circuitry), however you can achieve the same with software automation rules (i.e. when garage door opening, operate garage light).

rjblake, 2018-02-12:
Understand. My opener has a 12V 20W GU5.3  and  has a built in timer (up to 15mins). Rather than rely on this, I'll have a look at what I need to adjust in the code to rely solely on the GPIO to turn on/off the light

washcroft, 2018-02-12:
There's nothing you need to do, set the light input pin to a pin you're not using (ensure it's a pin pulled down by the chip) and then the only way your light output pin will trigger is when requested via the API.

mattiasclaesson, 2018-03-16:
Hi,

Are you sure its released in 2.0.1?

Because I get the same issue still:
/usr/local/lib/node_modules/homebridge-http-garagedoorcontroller/index.js:642                                                                                                                                                         
                this.garageLightCurrentState.setValue(this._lightCurrentState);                                                                                                                                                       
                                             ^                                                                                                                                                                                        
                                                                                                                                                                                                                                      
TypeError: Cannot read property 'setValue' of undefined                                                                                                                                                                               
    at HttpGarageDoorControllerAccessory._setLightCurrentState (/usr/local/lib/node_modules/homebridge-http-garagedoorcontroller/index.js:642:32)

----------------
Loading 2 accessories...                                                                                                                                                                                         
[2018-3-16 22:00:52] [Dörr] Initializing HttpGarageDoorController accessory...                                                                                                                                                        
[2018-3-16 22:00:52] [Dörr] Starting HttpGarageDoorControllerAccessory v2.0.1                                                                                                                                                         
[2018-3-16 22:00:52] [Dörr] INITIAL Garage Door state is: CLOSED                                                                                                                                                                      
[2018-3-16 22:00:52] [Dörr] INITIAL Garage Door target state is: CLOSED

Or do I need to do something more to get the new version loaded?

/Mattias

washcroft, 2018-03-19:
@mattiasclaesson Yes, but maybe this is a different issue... Can you share your homebridge config for the plugin (masking any sensitive info) and share a typical response from your garage door controller for the door state check (if not using the accompanying Arduino project).

mattiasclaesson, 2018-03-19:
@washcroft
Maybe its homekit that has a light configured from before, so it asks homebridge?
I guess I should remove it from the homebridge accessories from that side first, right?

The callstack seem to indictate that there is a request for outside.

/M

TypeError: Cannot read property 'setValue' of undefined                                                                                
    at HttpGarageDoorControllerAccessory._setLightCurrentState (/usr/local/lib/node_modules/homebridge-http-garagedoorcontroller/index.js:642:3
2)                                                                                                                                     
    at /usr/local/lib/node_modules/homebridge-http-garagedoorcontroller/index.js:482:13                                                
    at /usr/local/lib/node_modules/homebridge-http-garagedoorcontroller/index.js:552:4                                                 
    at Request._callback (/usr/local/lib/node_modules/homebridge-http-garagedoorcontroller/index.js:831:5)                             
    at Request.self.callback (/usr/local/lib/node_modules/homebridge-http-garagedoorcontroller/node_modules/request/request.js:186:22) 
    at Request.emit (events.js:159:13)                                                                                                 
    at Request.<anonymous> (/usr/local/lib/node_modules/homebridge-http-garagedoorcontroller/node_modules/request/request.js:1163:10)  
    at Request.emit (events.js:159:13)                                                                                                 
    at IncomingMessage.<anonymous> (/usr/local/lib/node_modules/homebridge-http-garagedoorcontroller/node_modules/request/request.js:1085:12)
    at Object.onceWrapper (events.js:254:19)

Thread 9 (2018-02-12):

Compile errors

rjblake, 2018-02-12:
Just downloaded the zip and tried to compile for an ESP8266. Arduino IDE came back with a whole stack of errors (well mostly warnings that result in errors), and an error. Guess I've got something wrong somewhere

Arduino: 1.8.5 (Mac OS X), Board: "Adafruit HUZZAH ESP8266, 80 MHz, 4M (1M SPIFFS), v2 Prebuilt (MSS=536), Disabled, None, 115200"

**Error:
sketch/src/HttpWebServer/HttpWebServer.cpp:405:87: error: no matching function for call to 'min(size_t, uint16_t&)'
         size_t oauth_nonce_length = min(strlen(q_oauth_nonce), this->_oauth_nonce_size);**

**Warnings (will look to rewrite the #ifdef)**
In file included from sketch/GarageDoorController.h:16:0,
                 from sketch/GarageDoorController.cpp:25:
sketch/src/Utilities/Utilities.h:11:18: warning: extra tokens at end of #ifdef directive [enabled by default]
 #ifdef LOG_LEVEL && LOG_LEVEL >= 1

                  ^
In file included from sketch/src/HttpWebServer/../../src/Sha/sha256.h:4:0,
                 from sketch/src/HttpWebServer/HttpWebServer.h:18,
                 from sketch/GarageDoorController.h:17,
                 from sketch/GarageDoorController.cpp:25:
sketch/src/HttpWebServer/../../src/Sha/sha256_config.h:36:0: warning: "HASH_LENGTH" redefined [enabled by default]
 #define HASH_LENGTH 32
 ^
In file included from sketch/src/HttpWebServer/../../src/Sha/sha1.h:4:0,
                 from sketch/src/HttpWebServer/HttpWebServer.h:17,
                 from sketch/GarageDoorController.h:17,
                 from sketch/GarageDoorController.cpp:25:
sketch/src/HttpWebServer/../../src/Sha/sha1_config.h:38:0: note: this is the location of the previous definition
 #define HASH_LENGTH 20
 ^
sketch/GarageDoorController.cpp:322:18: warning: extra tokens at end of #ifdef directive [enabled by default]
 #ifdef LOG_LEVEL && LOG_LEVEL >= 3

                  ^
In file included from sketch/GarageDoorController.h:13:0,
                 from sketch/GarageDoorController.cpp:25:
sketch/config.h:11:39: warning: large integer implicitly truncated to unsigned type [-Woverflow]
 const uint16_t DOOR_AUTO_CLOSE_TIME = 300000;

                                       ^
sketch/config.h:31:50: warning: large integer implicitly truncated to unsigned type [-Woverflow]
 const uint16_t OAUTH_TIMESTAMP_VALIDITY_WINDOW = 300000;

                                                  ^
In file included from sketch/GarageDoorController.h:16:0,
                 from /Users/richard/Documents/Arduino/HttpGarageDoorController/HttpGarageDoorController.ino:46:
sketch/src/Utilities/Utilities.h:11:18: warning: extra tokens at end of #ifdef directive [enabled by default]
 #ifdef LOG_LEVEL && LOG_LEVEL >= 1

                  ^
In file included from sketch/src/HttpWebServer/../../src/Sha/sha256.h:4:0,
                 from sketch/src/HttpWebServer/HttpWebServer.h:18,
                 from sketch/GarageDoorController.h:17,
                 from /Users/richard/Documents/Arduino/HttpGarageDoorController/HttpGarageDoorController.ino:46:
sketch/src/HttpWebServer/../../src/Sha/sha256_config.h:36:0: warning: "HASH_LENGTH" redefined [enabled by default]
 #define HASH_LENGTH 32
 ^
In file included from sketch/src/HttpWebServer/../../src/Sha/sha1.h:4:0,
                 from sketch/src/HttpWebServer/HttpWebServer.h:17,
                 from sketch/GarageDoorController.h:17,
                 from /Users/richard/Documents/Arduino/HttpGarageDoorController/HttpGarageDoorController.ino:46:
sketch/src/HttpWebServer/../../src/Sha/sha1_config.h:38:0: note: this is the location of the previous definition
 #define HASH_LENGTH 20
 ^
In file included from /Users/richard/Documents/Arduino/HttpGarageDoorController/HttpGarageDoorController.ino:43:0:
sketch/config.h:11:39: warning: large integer implicitly truncated to unsigned type [-Woverflow]
 const uint16_t DOOR_AUTO_CLOSE_TIME = 300000;

                                       ^
sketch/config.h:31:50: warning: large integer implicitly truncated to unsigned type [-Woverflow]
 const uint16_t OAUTH_TIMESTAMP_VALIDITY_WINDOW = 300000;

                                                  ^
/Users/richard/Documents/Arduino/HttpGarageDoorController/HttpGarageDoorController.ino: In function 'void loop()':
/Users/richard/Documents/Arduino/HttpGarageDoorController/HttpGarageDoorController.ino:205:19: warning: converting to non-pointer type 'int' from NULL [-Wconversion-null]
     if (client != NULL) {
                   ^
In file included from sketch/src/HttpWebServer/HttpWebServer.h:14:0,
                 from sketch/src/HttpWebServer/HttpWebServer.cpp:25:
sketch/src/HttpWebServer/../../src/Utilities/Utilities.h:11:18: warning: extra tokens at end of #ifdef directive [enabled by default]
 #ifdef LOG_LEVEL && LOG_LEVEL >= 1

                  ^
In file included from sketch/src/HttpWebServer/../../src/Sha/sha256.h:4:0,
                 from sketch/src/HttpWebServer/HttpWebServer.h:18,
                 from sketch/src/HttpWebServer/HttpWebServer.cpp:25:
sketch/src/HttpWebServer/../../src/Sha/sha256_config.h:36:0: warning: "HASH_LENGTH" redefined [enabled by default]
 #define HASH_LENGTH 32
 ^
In file included from sketch/src/HttpWebServer/../../src/Sha/sha1.h:4:0,
                 from sketch/src/HttpWebServer/HttpWebServer.h:17,
                 from sketch/src/HttpWebServer/HttpWebServer.cpp:25:
sketch/src/HttpWebServer/../../src/Sha/sha1_config.h:38:0: note: this is the location of the previous definition
 #define HASH_LENGTH 20
 ^
sketch/src/HttpWebServer/HttpWebServer.cpp: In member function 'void HttpWebServer::poll(Client&, uint16_t (*)(Client&, const char*, const char*, HashMap<char*, char*, 24u>&))':
sketch/src/HttpWebServer/HttpWebServer.cpp:264:85: warning: passing NULL to non-pointer argument 3 of 'size_t percent_decode(const char*, char*, size_t)' [-Wconversion-null]
           size_t name_decoded_size = percent_decode(query_parameter_name, NULL, NULL);

                                                                                     ^
sketch/src/HttpWebServer/HttpWebServer.cpp:269:87: warning: passing NULL to non-pointer argument 3 of 'size_t percent_decode(const char*, char*, size_t)' [-Wconversion-null]
           size_t value_decoded_size = percent_decode(query_parameter_value, NULL, NULL);

                                                                                       ^
sketch/src/HttpWebServer/HttpWebServer.cpp:339:90: warning: deprecated conversion from string constant to 'char*' [-Wwrite-strings]
         bool oauth_parameters_receieved = request_query_map.contains("oauth_consumer_key") && request_query_map.contains("oauth_signature") && request_query_map.contains("oauth_signature_method") && request_query_map.contains("oauth_timestamp") && request_query_map.contains("oauth_nonce");

                                                                                          ^
sketch/src/HttpWebServer/HttpWebServer.cpp:339:139: warning: deprecated conversion from string constant to 'char*' [-Wwrite-strings]
         bool oauth_parameters_receieved = request_query_map.contains("oauth_consumer_key") && request_query_map.contains("oauth_signature") && request_query_map.contains("oauth_signature_method") && request_query_map.contains("oauth_timestamp") && request_query_map.contains("oauth_nonce");

                                                                                                                                           ^
sketch/src/HttpWebServer/HttpWebServer.cpp:339:195: warning: deprecated conversion from string constant to 'char*' [-Wwrite-strings]
         bool oauth_parameters_receieved = request_query_map.contains("oauth_consumer_key") && request_query_map.contains("oauth_signature") && request_query_map.contains("oauth_signature_method") && request_query_map.contains("oauth_timestamp") && request_query_map.contains("oauth_nonce");

                                                                                                                                                                                                   ^
sketch/src/HttpWebServer/HttpWebServer.cpp:339:244: warning: deprecated conversion from string constant to 'char*' [-Wwrite-strings]
         bool oauth_parameters_receieved = request_query_map.contains("oauth_consumer_key") && request_query_map.contains("oauth_signature") && request_query_map.contains("oauth_signature_method") && request_query_map.contains("oauth_timestamp") && request_query_map.contains("oauth_nonce");

                                                                                                                                                                                                                                                    ^
sketch/src/HttpWebServer/HttpWebServer.cpp:339:289: warning: deprecated conversion from string constant to 'char*' [-Wwrite-strings]
         bool oauth_parameters_receieved = request_query_map.contains("oauth_consumer_key") && request_query_map.contains("oauth_signature") && request_query_map.contains("oauth_signature_method") && request_query_map.contains("oauth_timestamp") && request_query_map.contains("oauth_nonce");

                                                                                                                                                                                                                                                                                                 ^
sketch/src/HttpWebServer/HttpWebServer.cpp:345:72: warning: deprecated conversion from string constant to 'char*' [-Wwrite-strings]
           q_oauth_consumer_key = request_query_map["oauth_consumer_key"];

                                                                        ^
sketch/src/HttpWebServer/HttpWebServer.cpp:346:66: warning: deprecated conversion from string constant to 'char*' [-Wwrite-strings]
           q_oauth_signature = request_query_map["oauth_signature"];

                                                                  ^
sketch/src/HttpWebServer/HttpWebServer.cpp:347:80: warning: deprecated conversion from string constant to 'char*' [-Wwrite-strings]
           q_oauth_signature_method = request_query_map["oauth_signature_method"];

                                                                                ^
sketch/src/HttpWebServer/HttpWebServer.cpp:348:66: warning: deprecated conversion from string constant to 'char*' [-Wwrite-strings]
           q_oauth_timestamp = request_query_map["oauth_timestamp"];

                                                                  ^
sketch/src/HttpWebServer/HttpWebServer.cpp:349:58: warning: deprecated conversion from string constant to 'char*' [-Wwrite-strings]
           q_oauth_nonce = request_query_map["oauth_nonce"];
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
sparklingsparklers, 2018-02-21:
Ever get to the bottom of this?

washcroft, 2018-02-27:
@rjblake @sparklingsparklers fixed in the latest commit, issue caused by changes in ESP8266 release v2.4

Closed 2018-02-27.

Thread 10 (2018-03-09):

Enhancement Request: Add temperature sensor support (e.g. DHT22, BME280, etc.)

rjblake, 2018-03-09:
Still waiting for me eBay relay delivery and was thinking it might be nice to also be able to have the temperature of the garage reported. Haven't managed to wrap my head around how to include in the webserver and also to the Homebridge setup.

rjblake, 2018-03-27:
Problem sorted with the relay (triggered high version). I've added an SHT31 (temperature & humidity sensor) and adjusted the code to work with this. I considered a DHT22, but the reaction time is slow, so thought it better to go with a more 'reactive' sensor. However, I need to look at your accompanying Homebridge code to include reading of the sensor; as only in test mode still and have not included the OAuth authentication (i.e. only reads info when not secure). Once I've got this sorted, I'll create a new fork and submit pull request if you want to include.

rjblake, 2018-04-17:
Have had little time to look into this, but have pondered an alternative approach. As I'm using Domoticz for other purposes and it does a good job of pulling various different HA aspects together, it may make more sense in my case to look into using MQTT to at least publish information on door-state, light-state and temp/humidity to Domoticz so I have visibility there too (Homekit/Homebridge does not provide cover for all the devices/type of devices I have) and have an option of a more comprehensive approach. Now need to see where I need to add relevant MQTT pub/sub code without breaking it

washcroft, 2018-05-23:
Adding support for a temperature sensor is a good idea, to complement the light "addon". This and MQTT status publishing is on my todo list.

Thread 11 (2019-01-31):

error on compile.

lagunacomputer, 2019-01-31:
how can I fix?

sketch\GarageDoorController.cpp: In member function 'void GarageDoorController::getJsonStatus(char*, size_t)':

GarageDoorController.cpp:149: error: 'StaticJsonBuffer' was not declared in this scope

   StaticJsonBuffer<200> jsonBuffer;

   ^

GarageDoorController.cpp:149: error: 'jsonBuffer' was not declared in this scope

   StaticJsonBuffer<200> jsonBuffer;

                         ^

GarageDoorController.cpp:162: error: 'ArduinoJson::JsonObject' has no member named 'printTo'

   jsonRoot.printTo(dest, destSize);

            ^

exit status 1
'StaticJsonBuffer' was not declared in this scope

lagunacomputer, 2019-01-31:
fixed this by downgrading to library ArduinoJson 5.13.4 from version 6beta in the Arduino IDE library manager

Closed 2019-01-31.

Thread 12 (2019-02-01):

i fixed Homebridge "...cannot find garagedoorcontroller.local:80" etc by editing hosts file on pi

lagunacomputer, 2019-02-01:
i fixed Homebridge "...cannot find garagedoorcontroller.local:80" etc by editing hosts file on pi

I could not figure out why my NodeMCU/ESP8266 would disconnect and reconnect, I thought it was a problem with wifi reception but it wasn't.

Turns out mdns/avahi stops finding the dns name "garagedoorcontroller.local" quite often in my case.
Simply adding the ip and dns name as a host file entry on my raspberry pi running HomeBridge was the answer.  My ip of my arduino is 192.168.1.59, so i added the line "192.168.1.59      garagedoorcontroller.local" to my /etc/hosts file using the sudo nano /etc/hosts command, and BAMO, HomeBridge could find the device every time and no more errors.

Obviously you want a static IP on the arduino or a DHCP reservation in your router so that it always gets the same ip.  If the arduino or ESP8266 ip should change, you would need to change it in hosts file too.

Hope this helps someone, I struggled for hours with this.

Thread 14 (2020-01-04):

starts with relays on, how can i flip the default pin state easily?

lagunacomputer, 2020-01-04:
Hey Warren everything works great, been using this for over a year now.  But im having trouble when my controller is powered on, it flips the relays to an 'on' state, thus operating the door when unwanted.

I'm looking at the code, but cant find an easy answer.  How can I flip the default state of the door and light output pins to ensure they are 'off' instead of 'on' ?

thanks for your time sir.

rjblake, 2020-01-05:
Seem to recall I had same issue initially. Problem was solved with a different relay

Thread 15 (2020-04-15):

Compiling Issues Arduino Library

jeylites, 2020-04-15:
@washcroft

I hope all is well during these uncharted times.  I needed to change my Wemos D1 earlier today, tried to compile only to run into some errors.

It seems that there's an incompatibility issue with ArduinoJson library. So I downgraded to ver.5 which has to lead me to another problem with WifiHelper

**ArduinoJson Issue**

```
HttpGarageDoorController:146:11: error: StaticJsonBuffer is a class from ArduinoJson 5. Please see arduinojson.org/upgrade to learn how to upgrade your program to ArduinoJson version 6
   StaticJsonBuffer<200> jsonBuffer;
           ^
exit status 1
StaticJsonBuffer is a class from ArduinoJson 5. Please see arduinojson.org/upgrade to learn how to upgrade your program to ArduinoJson version 6

```

**Wifihelper Issue**

```

sketch/src/WiFiHelper/WiFiHelper.cpp: In member function 'bool WiFiHelper::connect()':
sketch/src/WiFiHelper/WiFiHelper.cpp:202:23: error: ambiguous overload for 'operator!=' (operand types are 'wl_status_t' and 'const IPAddress')
     if (WiFi.status() != INADDR_NONE) {

                       ^
sketch/src/WiFiHelper/WiFiHelper.cpp:202:23: note: candidates are:
sketch/src/WiFiHelper/WiFiHelper.cpp:202:23: note: operator!=(int, uint32_t {aka unsigned int}) <built-in>
sketch/src/WiFiHelper/WiFiHelper.cpp:202:23: note: operator!=(int, u32_t {aka long unsigned int}) <built-in>
sketch/src/WiFiHelper/WiFiHelper.cpp:202:23: note: operator!=(int, int) <built-in>
exit status 1
Error compiling for board LOLIN(WEMOS) D1 R2 & mini.
```

jeylites, 2020-04-17:
@washcroft

I was able to recompile based on the following version but it would be nice to have an updated version.

WifiHelper issue was due to the ESP Board Version. Only works on 2.4.2, anything above would give an error.

**HttpGarageDoorController**
HTTP Controller Firmware Version 2.0.0

**Arduino Library**
ArduinoJson  Version 5.1.0
Arduino OTA Version 1.0.0
Wifi101 Version 0.11.2
Wifi 101 OTA Version  1.0.0

**Board Manager**
ESP8266 Version  2.4.2

**Arduino Compiler**
Version 1.8.12 MacOsx

jeylites, 2020-05-07:
@washcroft

Hello, just checking in....

jeylites, 2021-09-14:
Hello, Any thoughts on updating this lovely project? I still can't get it to work with my garage door. :(

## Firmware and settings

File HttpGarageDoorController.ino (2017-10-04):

/*
MIT License

Copyright (c) 2017 Warren Ashcroft

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
THE SOFTWARE IS PROVIDED "AS IS", WITHOUT WARRANTY OF ANY KIND, EXPRESS OR
IMPLIED, INCLUDING BUT NOT LIMITED TO THE WARRANTIES OF MERCHANTABILITY,
FITNESS FOR A PARTICULAR PURPOSE AND NONINFRINGEMENT. IN NO EVENT SHALL THE
AUTHORS OR COPYRIGHT HOLDERS BE LIABLE FOR ANY CLAIM, DAMAGES OR OTHER
LIABILITY, WHETHER IN AN ACTION OF CONTRACT, TORT OR OTHERWISE, ARISING FROM,
OUT OF OR IN CONNECTION WITH THE SOFTWARE OR THE USE OR OTHER DEALINGS IN THE
SOFTWARE.
*/

#define CONTROLLER_MODEL "GARAGEDOOR"
#define CONTROLLER_FIRMWARE_VERSION "2.0.0"

// ARDUINO LIBRARIES
#include <Arduino.h>

#ifdef ESP8266
  #include <ArduinoOTA.h>
#else
  #include <WiFi101OTA.h>
#endif

#include <WiFiClient.h>
#include <WiFiServer.h>


// INCLUDES
#include "compile.h"
#include "config.h"
#include "secret.h"

#include "GarageDoorController.h"
GarageDoorController gController;

#include "src/WiFiHelper/WiFiHelper.h"
#include "src/HttpWebServer/HttpWebServer.h"

#ifdef ENABLE_HTTP_SERVER_OAUTH_AUTH
  #include <WiFiUdp.h>
  WiFiUDP gUdp;
#endif


// GLOBAL VARIABLES
WiFiHelper gWiFiHelper(MDNS_NAME, WIFI_SSID, WIFI_PASSWORD, WIFI_CONNECTION_TIMEOUT);
WiFiServer gServer(HTTP_SERVER_PORT);
HttpWebServer gHttpWebServer(gServer, HTTP_SERVER_PORT, HTTP_REQUEST_TIMEOUT, HTTP_REQUEST_BUFFER_SIZE);


// SETUP
void setup()
{
#if LOG_LEVEL > 0
  delay(5000); // Allow time for serial monitor connection

  // Open serial port for debug
  Serial.begin(115200);
  Serial.println("Started Serial Debug");
#endif

  LOGPRINTLN_TRACE("Entered setup()");
  gWiFiHelper.enable_led(LED_BUILTIN, LED_BUILTIN_ON, LED_BUILTIN_OFF, false);

#ifdef ENABLE_HTTP_SERVER_APIKEY_HEADER_AUTH
  gHttpWebServer.enable_apikey_header_auth(HTTP_SERVER_APIKEY_HEADER);
#endif

#ifdef ENABLE_HTTP_SERVER_OAUTH_AUTH
  gHttpWebServer.enable_oauth_auth(gUdp, HTTP_SERVER_OAUTH_CONSUMER_KEY, HTTP_SERVER_OAUTH_CONSUMER_SECRET, OAUTH_NONCE_SIZE, OAUTH_NONCE_HISTORY, OAUTH_TIMESTAMP_VALIDITY_WINDOW);
#endif

  // Setup Controller
  gController.setup();
}


// METHODS
bool connectWiFi()
{
  LOGPRINTLN_TRACE("Entered connectWiFi()");

  if (gWiFiHelper.is_connected()) {
    return true;
  }

  if (!gWiFiHelper.connect()) {
    return false;
  }

  // Start OTA updater / mDNS responder
  LOGPRINT_INFO("Starting OTA updater / mDNS responder");

#ifdef ESP8266
  ArduinoOTA.setHostname(MDNS_NAME);
  ArduinoOTA.setPassword(OTA_UPDATER_PASSWORD);
  ArduinoOTA.begin();
#else

  if (!WiFiOTA.begin(MDNS_NAME, OTA_UPDATER_PASSWORD, InternalStorage)) {
    LOGPRINTLN_INFO("...failed!");
  } else {
    LOGPRINTLN_INFO("...started!");
  }

#endif

  // Start HTTP web server
  LOGPRINT_INFO("Starting HTTP web server...");
  gHttpWebServer.begin();
  LOGPRINTLN_INFO("started!");

#ifdef ENABLE_HTTP_SERVER_OAUTH_AUTH
  LOGPRINT_INFO("Initalising clock...");

  if (!gHttpWebServer.clock->update(true)) {
    LOGPRINTLN_INFO("failed!");
  } else {
    LOGPRINT_INFO("initalised at ");

    char formattedTime[20];
    gHttpWebServer.clock->get_formatted_time(gHttpWebServer.clock->now_utc(), formattedTime, sizeof(formattedTime));
    LOGPRINT_INFO(formattedTime);
    LOGPRINTLN_INFO(" UTC");
  }

#endif
}

void getJsonDeviceInfo(char *const jsonDeviceInfo, size_t jsonDeviceInfoSize)
{
  LOGPRINTLN_VERBOSE("Entered getJsonDeviceInfo()");
  StaticJsonBuffer<200> jsonBuffer;
  JsonObject &jsonRoot = jsonBuffer.createObject();

  char mac[18] = {0};
  gWiFiHelper.get_mac(mac, sizeof(mac));

  char ip[16] = {0};
  gWiFiHelper.get_client_ip(ip, sizeof(ip));

  jsonRoot["mdns"] = MDNS_NAME;
  jsonRoot["name"] = FRIENDLY_NAME;
  jsonRoot["model"] = CONTROLLER_MODEL;
  jsonRoot["firmware"] = CONTROLLER_FIRMWARE_VERSION;
  jsonRoot["ip"] = ip;
  jsonRoot["mac"] = mac;

  jsonRoot.printTo(jsonDeviceInfo, jsonDeviceInfoSize);
}

uint16_t requestHandler(Client &client, const char *requestMethod, const char *requestUrl, HashMap<char *, char *, 24> &requestQuery)
{
  if ((strcmp(requestMethod, "GET") == 0) && (strcasecmp(requestUrl, "/device") == 0)) {
    char jsonDeviceInfo[256];
    getJsonDeviceInfo(jsonDeviceInfo, sizeof(jsonDeviceInfo));
    HttpWebServer::send_response(client, 200, (uint8_t *)jsonDeviceInfo, strlen(jsonDeviceInfo));
    return 0;
  }
  
  return gController.requestHandler(client, requestMethod, requestUrl, requestQuery);
}

// MAIN LOOP
void loop()
{
  LOGPRINTLN_TRACE("Entered loop()");

  // Check/reattempt connection to WiFi
  LOGPRINTLN_TRACE("Calling connectWiFi()");
  bool connected = connectWiFi();

  // Loop Controller
  gController.loop();

  if (connected) {
    // Handle incoming mDNS/OTA requests
    LOGPRINTLN_TRACE("Calling WiFiOTA.poll()");

#ifdef ESP8266
    ArduinoOTA.handle();
#else
    WiFiOTA.poll();
#endif

    // Handle incoming HTTP/aREST requests
    LOGPRINTLN_TRACE("Calling gHttpWebServer.poll()");
    WiFiClient client = gServer.available();

#ifdef ESP8266

    if (client != NULL) {
      LOGPRINT_INFO("\nAccepted new client connection from ");
      LOGPRINT_INFO((IPAddress)client.remoteIP());
      LOGPRINT_INFO(":");
      LOGPRINTLN_INFO(client.remotePort());
    }

#endif

    gHttpWebServer.poll(client, requestHandler);
  }
}

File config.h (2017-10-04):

#ifndef CONFIG_H
#define CONFIG_H

// Controller Config
const char MDNS_NAME[] = "garagedoorcontroller";
const char FRIENDLY_NAME[] = "Garage Door Controller";
const uint16_t DOOR_OUTPUT_PULSE_TIME = 400;
const uint16_t DOOR_OUTPUT_PULSE_DELAY_TIME = 1250;
const uint16_t DOOR_SENSOR_REACT_TIME = 3000;
const uint16_t DOOR_MAX_OPEN_CLOSE_TIME = 25000;
const uint16_t DOOR_AUTO_CLOSE_TIME = 300000;

// GPIO Pins
const uint8_t LED_OUTPUT_PIN = LED_BUILTIN;
const uint8_t DOOR_OUTPUT_OPEN_PIN = 3;
const uint8_t DOOR_OUTPUT_CLOSE_PIN = 3;
const uint8_t LIGHT_OUTPUT_PIN = 2;
const uint8_t LIGHT_INPUT_PIN = 1;
const uint8_t SENSOR_OPEN_INPUT_PIN = 5;
const uint8_t SENSOR_CLOSED_INPUT_PIN = 4;

// Network Config
const uint16_t HTTP_SERVER_PORT = 80;
const uint16_t HTTP_REQUEST_TIMEOUT = 4000;
const uint16_t HTTP_REQUEST_BUFFER_SIZE = 512;
const uint16_t WIFI_CONNECTION_TIMEOUT = 10000;

// OAuth Config
const uint16_t OAUTH_NONCE_SIZE = 24;
const uint16_t OAUTH_NONCE_HISTORY = 255;
const uint16_t OAUTH_TIMESTAMP_VALIDITY_WINDOW = 300000;

#endif // CONFIG

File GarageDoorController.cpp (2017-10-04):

/*
MIT License

Copyright (c) 2017 Warren Ashcroft

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
THE SOFTWARE IS PROVIDED "AS IS", WITHOUT WARRANTY OF ANY KIND, EXPRESS OR
IMPLIED, INCLUDING BUT NOT LIMITED TO THE WARRANTIES OF MERCHANTABILITY,
FITNESS FOR A PARTICULAR PURPOSE AND NONINFRINGEMENT. IN NO EVENT SHALL THE
AUTHORS OR COPYRIGHT HOLDERS BE LIABLE FOR ANY CLAIM, DAMAGES OR OTHER
LIABILITY, WHETHER IN AN ACTION OF CONTRACT, TORT OR OTHERWISE, ARISING FROM,
OUT OF OR IN CONNECTION WITH THE SOFTWARE OR THE USE OR OTHER DEALINGS IN THE
SOFTWARE.
*/

#include "GarageDoorController.h"

GarageDoorController::GarageDoorController()
{
  this->_sensorOpenDebouncer = new Bounce();
  this->_sensorClosedDebouncer = new Bounce();
  this->_lightInputDebouncer = new Bounce();
}

GarageDoorController::~GarageDoorController()
{
}

void GarageDoorController::setup()
{
  // Configure input pins and debouncing
  pinMode(SENSOR_OPEN_INPUT_PIN, INPUT_PULLUP);
  this->_sensorOpenDebouncer->attach(SENSOR_OPEN_INPUT_PIN);
  this->_sensorOpenDebouncer->interval(50);

  pinMode(SENSOR_CLOSED_INPUT_PIN, INPUT_PULLUP);
  this->_sensorClosedDebouncer->attach(SENSOR_CLOSED_INPUT_PIN);
  this->_sensorClosedDebouncer->interval(50);

  pinMode(LIGHT_INPUT_PIN, INPUT_PULLUP);
  this->_lightInputDebouncer->attach(LIGHT_INPUT_PIN);
  this->_lightInputDebouncer->interval(50);

  // Configure output pins
  pinMode(LED_OUTPUT_PIN, OUTPUT);
  digitalWrite(LED_OUTPUT_PIN, LED_BUILTIN_OFF);

  pinMode(DOOR_OUTPUT_OPEN_PIN, OUTPUT);
  pinMode(DOOR_OUTPUT_CLOSE_PIN, OUTPUT);
  pinMode(LIGHT_OUTPUT_PIN, OUTPUT);
}

void GarageDoorController::loop()
{
  // Handle debouncing
  LOGPRINTLN_TRACE("Calling _debouncers.update()");
  this->_sensorOpenDebouncer->update();
  this->_sensorClosedDebouncer->update();
  this->_lightInputDebouncer->update();

  // Update states
  LOGPRINTLN_TRACE("Calling _monitorInputs()");
  this->_monitorInputs();
}

void GarageDoorController::operateDoor(bool state)
{
  LOGPRINTLN_VERBOSE("Entered operateDoor()");

  uint8_t pin = 0;
  uint8_t cycles = 0;
  uint8_t DOOR_OUTPUT_PIN = DOOR_OUTPUT_OPEN_PIN;

  if (state) {
    if (DOOR_OUTPUT_OPEN_PIN != DOOR_OUTPUT_CLOSE_PIN) {
      pin = DOOR_OUTPUT_OPEN_PIN;
      cycles = 1;

    } else if ((this->DoorState == DOORSTATE_CLOSED) || (this->DoorState == DOORSTATE_STOPPED_CLOSING) || (this->DoorState == DOORSTATE_UNKNOWN)) {
      pin = DOOR_OUTPUT_PIN;
      cycles = 1;

    } else if (this->DoorState == DOORSTATE_CLOSING) {
      pin = DOOR_OUTPUT_PIN;
      cycles = 2;

    } else if (this->DoorState == DOORSTATE_STOPPED_OPENING) {
      pin = DOOR_OUTPUT_PIN;
      cycles = 3;

    }

    this->DoorState = DOORSTATE_OPENING;

  } else {
    if (DOOR_OUTPUT_OPEN_PIN != DOOR_OUTPUT_CLOSE_PIN) {
      pin = DOOR_OUTPUT_CLOSE_PIN;
      cycles = 1;

    } else if ((this->DoorState == DOORSTATE_OPEN) || (this->DoorState == DOORSTATE_STOPPED_OPENING) || (this->DoorState == DOORSTATE_UNKNOWN)) {
      pin = DOOR_OUTPUT_PIN;
      cycles = 1;

    } else if (this->DoorState == DOORSTATE_OPENING) {
      pin = DOOR_OUTPUT_PIN;
      cycles = 2;

    } else if (this->DoorState == DOORSTATE_STOPPED_CLOSING) {
      pin = DOOR_OUTPUT_PIN;
      cycles = 3;

    }

    this->DoorState = DOORSTATE_CLOSING;
  }

  if ((pin > 0) && (cycles > 0)) {
    LOGPRINT_INFO("\nOUTPUT: Changing garage door state to: ");
    LOGPRINTLN_INFO(GarageDoorController::stringFromDoorState(this->DoorState));
    this->_operateDoor(pin, cycles);
  }
}

void GarageDoorController::switchLight(bool state)
{
  LOGPRINTLN_VERBOSE("Entered switchLight()");
  this->LightOutput = (bool)digitalRead(LIGHT_OUTPUT_PIN);

  if (this->LightOutput != state) {
    LOGPRINT_INFO("\nOUTPUT: Changing garage light state to: ");
    LOGPRINTLN_INFO(state);
    digitalWrite(LIGHT_OUTPUT_PIN, state);
  }
}

void GarageDoorController::getJsonStatus(char *const dest, size_t destSize)
{
  LOGPRINTLN_VERBOSE("Entered getJsonStatus()");
  StaticJsonBuffer<200> jsonBuffer;
  JsonObject &jsonRoot = jsonBuffer.createObject();

  jsonRoot["result"] = 200;
  jsonRoot["success"] = true;
  jsonRoot["message"] = "OK";
  jsonRoot["light-input"] = this->LightInput;
  jsonRoot["light-requested"] = this->LightRequested;
  jsonRoot["light-state"] = this->LightState;
  jsonRoot["sensor-open"] = this->SensorOpen;
  jsonRoot["sensor-closed"] = this->SensorClosed;
  jsonRoot["door-state"] = GarageDoorController::stringFromDoorState(this->DoorState);

  jsonRoot.printTo(dest, destSize);
}

uint16_t GarageDoorController::requestHandler(Client &client, const char *requestMethod, const char *requestUrl, HashMap<char *, char *, 24> &requestQuery)
{
  LOGPRINTLN_VERBOSE("Entered _requestHandler()");

  if (strcmp(requestMethod, "GET") == 0) {
    if (strcasecmp(requestUrl, "/controller") == 0) {
      char jsonStatus[256];
      this->getJsonStatus(jsonStatus, sizeof(jsonStatus));
      HttpWebServer::send_response(client, 200, (uint8_t *)jsonStatus, strlen(jsonStatus));
      return 0;

    } else {
      return 404;
    }
  } else if (strcmp(requestMethod, "PUT") == 0) {
    if ((strcasecmp(requestUrl, "/controller/light/on") == 0) || (strcasecmp(requestUrl, "/controller/light/off") == 0)) {
      if (striendswith(requestUrl, "/on")) {
        this->LightRequested = true;
      } else if (striendswith(requestUrl, "off")) {
        this->LightRequested = false;
      }

      // Switch the light
      this->LightState = (this->LightInput || this->LightRequested);
      this->switchLight(this->LightState);
      return 202;

    } else if ((strcasecmp(requestUrl, "/controller/door/open") == 0) || (strcasecmp(requestUrl, "/controller/door/close") == 0)) {
      bool doorOpen = false;

      if (striendswith(requestUrl, "/open")) {
        doorOpen = true;
      } else if (striendswith(requestUrl, "/close")) {
        doorOpen = false;
      }

      // Operate the door
      this->operateDoor(doorOpen);
      return 202;

    } else {
      return 404;
    }
  } else {
    return 405;
  }
}

char *GarageDoorController::stringFromDoorState(enum DoorState doorState)
{
  LOGPRINTLN_TRACE("Entered stringFromDoorState()");

  switch (doorState) {
    case DOORSTATE_OPEN:
      return (char *)"open";

    case DOORSTATE_CLOSED:
      return (char *)"closed";

    case DOORSTATE_OPENING:
      return (char *)"opening";

    case DOORSTATE_CLOSING:
      return (char *)"closing";

    case DOORSTATE_STOPPED_OPENING:
      return (char *)"stopped-opening";

    case DOORSTATE_STOPPED_CLOSING:
      return (char *)"stopped-closing";

    case DOORSTATE_UNKNOWN:
      return (char *)"unknown";

    default:
      return (char *)"unknown";
  }
}
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

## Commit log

2017-04-10 Changed light input mode to pullup, added the Bounce2 debouncing library to smooth the light and sensor inputs and updated documentation
2017-04-15 Config and documentation improvements
    [Circuit Diagram.fzz]
2017-10-04 v2.0.0 Major OAuth/ESP8266 Update
    v2.0.0 is a major update with the project refactored to separate concerns into their own modules.
    - Added: OAuth authentication support
    - Added: ESP8266 board compilation support
    - Added: Over-The-Air (OTA) firmware update support
    - Added: New feature to automatically close door after set time
    - Added: New API command /device to get device info
    - Added: MIT license and credits
    - Improved: Complete refactor
    - Improved: Debug and logging
    - Improved: HTTP request processing
    - Improved: WiFi connection logic (no longer blocks processing)
    [Clock.h, GarageDoorController.cpp, HttpGarageDoorController.ino]
